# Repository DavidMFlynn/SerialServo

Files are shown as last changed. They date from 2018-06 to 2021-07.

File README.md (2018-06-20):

# SerialServo
Packet serial to R/C servo w/ absolute encoder
This is for one of my robot projects.
Features: TTL Serial interface, PWM output w/ 1/2 microsecond resolution, Current sensing, Absolute encoder SPI interface.
Features will be added as needed.
The Rev B PCB is being printed 6/19/2018

ToDo:

  Add params:

  Mode 4, Gripper control, closed value, open value
    Move toward close until reached or max current
    Open to open value
    OpenValue = FastRevVal, CloseValue = FastRevVal
    Speed is used for close only
    Open may be greater than or less than close, RevDirFlag?

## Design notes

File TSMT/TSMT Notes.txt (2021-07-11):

Terran Space Marine Transporter Notes (TSMT)
==========================================================================================
Body Jacks (Lifters)
	Home Switch is center of travel
	Positive rotation turns CW, CCW (Looking at the output shaft)
	Seek Home: Find the edge. Set zero. Go positive to turn the home switch off.
	Home sensor: OPB490P11Z, Active Low when light is blocked. (Positive, CW to unblock)
	Motor:iPower GBM5208H-200T a.k.a. GM5208-24, 11 pole pairs, 66 counts per rotation.
	Gear ratio 183:1, 12078 Counts per Rotation (33.55 per degree), 
		Safe zone: ±5368 (±160°) Counts from home
	
Addresses: (Serial Port/Device)
	01/03	Left front body mounted lifter (Sensored BLDC Drive, Position Mode)
	01/04	Left front track unit mounted lifter (Sensored BLDC Drive, Position Mode)
	01/05	Left front track unit drive (Sensored BLDC Drive, Torque Mode)
	
	01/06	Right front body mounted lifter (Sensored BLDC Drive, Position Mode)
	01/07	Right front track unit mounted lifter (Sensored BLDC Drive, Position Mode)
	01/08	Right front track unit drive (Sensored BLDC Drive, Torque Mode)
	
	??/??	Left rear body mounted lifter (Sensored BLDC Drive, Position Mode)
	??/??	Left rear track unit mounted lifter (Sensored BLDC Drive, Position Mode)
	??/??	Left rear track unit drive (Sensored BLDC Drive, Torque Mode)
	
	??/??	Right rear body mounted lifter (Sensored BLDC Drive, Position Mode)
	??/??	Right rear track unit mounted lifter (Sensored BLDC Drive, Position Mode)
	??/??	Right rear track unit drive (Sensored BLDC Drive, Torque Mode)
	
Lifter Motor Commutation
	OPB490P11Z (buffered, 10KΩ Pull Up)
	Red-1 Anode 470Ω to +5V
	Black-2 Cathode to GND
	White-3 Vcc to +5V
	Blue-4 Output (Low when blocked)
	Green-5 Ground to GND
		
	OPB492T11Z (inverted, 10KΩ Pull Up)
	Red-1 Anode 470Ω to +5V
	Black-2 Cathode to GND
	White-3 Vcc to +5V
	Blue-4 Output (High when blocked)
	Green-5 Ground to GND
	
	Sensored BLDC Motor Drive
	J4-1 +5V, RED 24AWG
	J4-2 GND, BLK 24AWG
	J4-3 Hall-U, YEL 24AWG
	J4-4 Hall-V, GRN 24AWG
	J4-5 Hall-W, BLU 24AWG
	
Home Switch
	J10-1 +5V, RED 24AWG
	J10-2 Signal, YEL 24AWG
	J10-3 GND, Black 24AWG

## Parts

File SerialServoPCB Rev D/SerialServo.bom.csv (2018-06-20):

Source | /Projects/SerialServo/SerialServoPCB/SerialServo.sch
Kicad Rev | Eeschema (5.0.0-rc2-80-gf95b77b)
Generated Date | Tuesday | June 19 | 2018 at 05:32:33 PM
Title | Serial Servo
Company | DMFE
Revision | B
Date Issue | 2018-06-19
Comment | TTL serial r/c servo controller
Reference | Value | Library | Library Ref
U1 | PIC16F1847-ISO | MCU_Microchip_PIC16 | PIC16F648A-ISO
J1 | Conn_01x04 | Connector_Generic | Conn_01x04
VR1 | L78L05_TO92 | Regulator_Linear | L78L05_TO92
VR2 | LM7805_TO220 | Regulator_Linear | LM7805_TO220
D5 | D | Device | D
SW1 | SW_Push | Switch | SW_Push
D1 | LED | Device | LED
R13 | 47K | Device | R
R12 | 1K0 | Device | R
C4 | 0.1uF | Device | C_Small
U2 | LM358A | Amplifier_Operational | LM358
D6 | D | Device | D
R6 | 0R200 1W | Device | R
C8 | 0.1uF | Device | C_Small
J4 | Conn_01x03 | Connector_Generic | Conn_01x03
R1 | 220R | Device | R
J3 | Conn_01x05 | Connector_Generic | Conn_01x05
SW2 | SW_Push | Switch | SW_Push
D2 | LED | Device | LED
R15 | 47K | Device | R
R14 | 1K0 | Device | R
SW3 | SW_Push | Switch | SW_Push
D3 | LED | Device | LED
R17 | 47K | Device | R
R16 | 1K0 | Device | R
C10 | 1uF | Device | C_Small
R10 | 47K | Device | R
R11 | 10K | Device | R
R9 | 100K | Device | R
R7 | 1K0 | Device | R
C7 | 0.1uF | Device | C_Small
C9 | 100uF | Device | CP1_Small
J2 | Conn_01x05 | Connector_Generic | Conn_01x05
C1 | 0.1uF | Device | C_Small
D4 | LED | Device | LED
R3 | 1K0 | Device | R
RV1 | 20K | Device | R_POT
C3 | 0.1uF | Device | C_Small
R2 | 1K0 | Device | R
R4 | 100K | Device | R
R5 | 10K | Device | R
C2 | 2.2uF | Device | CP1_Small
C5 | 2.2uF | Device | CP1_Small
C6 | 0.1uF | Device | C_Small
R21 | 1K0 | Device | R
J5 | Conn_01x03 | Connector_Generic | Conn_01x03
R18 | 1K0 | Device | R
J6 | Conn_01x03 | Connector_Generic | Conn_01x03
J7 | Conn_01x03 | Connector_Generic | Conn_01x03
R19 | 1K0 | Device | R
C12 | 0.1uF | Device | C_Small
R20 | 1K0 | Device | R
C13 | 0.1uF | Device | C_Small
C11 | 0.1uF | Device | C_Small
VR3 | LD1085 | Regulator_Linear | AZ1117-ADJ
J8 | Conn_01x02 | Connector_Generic | Conn_01x02
R22 | 120R | Device | R
R8 | RRR | Device | R
C14 | 0.1uF | Device | C_Small

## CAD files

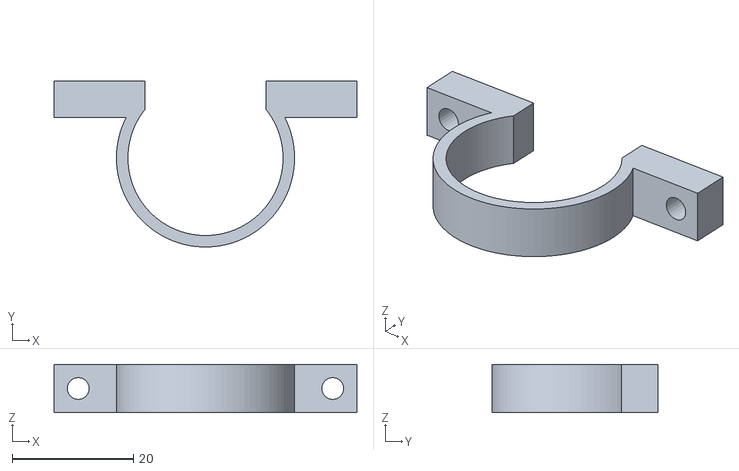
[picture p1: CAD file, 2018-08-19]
Case and Mount/Mount.stl
50.0 x 27.4 x 8.00

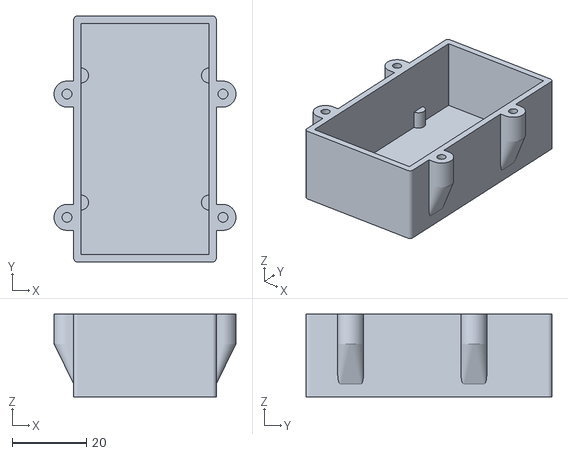
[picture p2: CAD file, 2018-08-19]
Case and Mount/Case.stl
49.0 x 66.2 x 22.3

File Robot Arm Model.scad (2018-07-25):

// ************************************************************
// Robot Arm Model
// David M. Flynn 
// Created: 6/11/2018
//
// Simple 3 degree of freedom arm
// Given an object (the blue sphere) at Obj_x,Obj_y,Obj_z
// Calculate the angle of the 3 joints (BaseRot_a,J1Rot_a,J2Rot_a)
// to place the object in the center of the gripper
// Recommended: Animation FPS=30, Steps=100 or more
// ************************************************************
//
// some usefull functions
function Oscillate(Dist) = (1-abs($t*2-1))*Dist; // move from 0 to Dist and back to 0 every cycle
function XY2Deg(X,Y) = -atan2(X,Y); // convert an X,Y to an angle 0=+y,90=-x,180/-180=-y,-90=+x
function Dist(X,Y) = sqrt(pow(X,2)+pow(Y,2)); // how far to x,y
//
//     C
//     /\
//   b/  \a
// A ----- B
//     c
// given the length of the sides calculate an inside angle
function AngleA(a,b,c) = acos( (pow(b,2)+pow(c,2)-pow(a,2)) / (2 * b * c));
function AngleB(a,b,c) = acos( (pow(a,2)+pow(c,2)-pow(b,2)) / (2 * a * c));
function AngleC(a,b,c) = acos( (pow(a,2)+pow(b,2)-pow(c,2)) / (2 * a * b));

//$t=0.0; // comment out to enable animation

// Position of object
Obj_x=Oscillate(200)-50;
Obj_y=Oscillate(100)+150;
Obj_z=Oscillate(100)+100; // from base plate or table surface

// The object.
translate([Obj_x,Obj_y,Obj_z]) color("Blue") sphere(d=20);

// Size of table base, just for show
	Table_h=3;
	Table_xy=200;

// Size of the joint, "A" has the servo and encoder, "B" is the turning part
	JointA_d=70;
	JointA_h=40;
	JointA_fn=14;
	JointB_d=90;
	JointB_h=38;
	JointB_fn=10;

// Length of the arm sections
	RodAB_l=240; // length from J1 to J2
	RodBC_l=230; // length from J2 center line to moddle of gripper
	
Tube_d=19;
BaseToJ1_z=JointB_d/2;
BaseToJ1_x=-JointA_h/2;
J1_CL_z=JointA_h+JointB_h+BaseToJ1_z;

module DrawJoint(Rot_a=0){
	// Base
	cylinder(d=JointA_d,h=JointA_h,$fn=JointA_fn);
	
	// the turning part
	translate([0,0,JointA_h]) rotate([0,0,Rot_a]){
		cylinder(d=JointB_d,h=JointB_h,$fn=JointB_fn);
		
		// Indicator: Which way am I pointing?
		translate([0,JointB_d/2-10,JointB_h]) rotate([0,0,-30]) color("Tan") cylinder(d=10,h=1,$fn=3);
	}
} // DrawJoint

module DrawBase(Rot_a=0){
	//translate([0,0,Table_h/2]) cylinder(d=Table_xy,h=Table_h,$fn=8,center=true);
	translate([0,0,-70]) cylinder(d1=120,d2=80,h=70,$fn=12);
	DrawJoint(Rot_a=Rot_a);
} // DrawBase

// do the math
BaseRot_a=XY2Deg(Obj_x,Obj_y);
Adj_z=Obj_z-J1_CL_z; // Z relitive to J1 rotation center
d=Dist(Obj_x,Obj_y);  // distance in XY plane
hypJ2=Dist(d,Adj_z); // end to J1 distance
Targ_a=XY2Deg(d,Adj_z);
J2Rot_a=180-AngleC(RodAB_l,RodBC_l,hypJ2);
J1Ang_B=AngleB(RodAB_l,RodBC_l,hypJ2);
J1Rot_a=Targ_a+J1Ang_B;

// Show the angles to the user.
echo(BaseRot=BaseRot_a);
echo(J1Rot_a=J1Rot_a);
echo(J2Rot_a=J2Rot_a);

// Draw the arm
module Draw3DoFArm(BaseRot_a=BaseRot_a,J1Rot_a=J1Rot_a,J2Rot_a=J2Rot_a){
	DrawBase(Rot_a=BaseRot_a);

	translate([0,0,JointA_h+JointB_h]) rotate([0,0,BaseRot_a]) translate([BaseToJ1_x,0,BaseToJ1_z])
		rotate([0,90,0]) rotate([0,0,90]){
			
		// the joint attached to the rotating base	
		DrawJoint(Rot_a=J1Rot_a);
			
		rotate([0,0,J1Rot_a]) translate([0,0,JointA_h+JointB_h/2]) {
			// rod connection J1 and J2
			rotate([-90,0,0]) color("Silver") cylinder(d=Tube_d,h=RodAB_l);
			translate([0,RodAB_l,JointA_h/2])rotate([0,180,0]){
				// mid-arm joint
				DrawJoint(Rot_a=J2Rot_a);
				// rod from J2 to middle of the gripper
				translate([0,0,JointA_h+JointB_h/2])rotate([0,0,J2Rot_a]){
					rotate([-90,0,0]) color("Silver") cylinder(d=Tube_d,h=RodBC_l);
}}}}}

//Draw3DoFArm();
//Draw3DoFArm(0,0,0);

// Lo-Rez Arm parts
module LoRezBase(){
	cylinder(d1=120,d2=80,h=70,$fn=12);
	translate([0,0,70]) cylinder(d=JointA_d,h=JointA_h,$fn=JointA_fn);
} // LoRezBase

//LoRezBase(); // height is 70+JointA_h

module LoRezJoint(){
	cylinder(d=JointB_d,h=JointB_h,$fn=JointB_fn);
		
		// Indicator: Which way am I pointing?
		translate([0,JointB_d/2-11,JointB_h]) rotate([0,0,-30]) color("Tan") cylinder(d=10,h=1,$fn=3);
} // LoRezJoint

//LoRezJoint();

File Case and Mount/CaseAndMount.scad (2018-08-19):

// ******************************************************
// Case and Mount for Serial Servo Rev B PCB
// by Dave Flynn
// Created:8/13/2018
// Revision: 1.0.1 8/19/2018
// Units: mm
// ******************************************************
// History:
// 1.0.1 8/19/2018 Moved mounting locations.
// 1.0.0 8/13/2018 First Code
// ******************************************************
// Notes:
// ******************************************************
// for STL output
// SSCaseBack();
// TubeMount();
// ******************************************************

include<CommonStuffSAEmm.scad>

$fn=90;
Overlap=0.05;
IDXtra=0.2;

PCB_x=34.4;
PCB_y=62.2;
PCB_z=1.8; // board only
PCB_Back_Parts_z=5;
PCB_Front_Parts_z=13.5;

CaseWall=2;
RC_BoltSpace=42;
Tube_OD=25.4;
RC_Spacer_h=4;

module RoundRect(X=60,Y=40,Z=10,R=5){
	hull(){
		translate([-X/2+R,-Y/2+R,0]) cylinder(r=R,h=Z);
		translate([X/2-R,-Y/2+R,0]) cylinder(r=R,h=Z);
		translate([-X/2+R,Y/2-R,0]) cylinder(r=R,h=Z);
		translate([X/2-R,Y/2-R,0]) cylinder(r=R,h=Z);
		
	} // hull
	
} // RoundRect

module SSCaseBack(){
	PCB_Clip_y=14;
	BoltBoss_yt=19;
	BoltBoss_yb=10;
	
	Case_h=PCB_Back_Parts_z+PCB_z+PCB_Front_Parts_z+CaseWall;
	
	module BoltBoss(XTra=1){
		difference(){
			hull(){
				translate([2.5+XTra,-3.5,0]) cube([Overlap,7,Case_h]);
				translate([0,0,Case_h-8]) cylinder(d=7,h=8);
			} // hull
			translate([0,0,Case_h])  Bolt4Hole(depth=9);
		} // diff
	}// BoltBoss
	
	difference(){
		RoundRect(X=PCB_x+CaseWall*2,Y=PCB_y+CaseWall*2,Z=Case_h,R=1);
		
		translate([0,0,CaseWall]) RoundRect(X=PCB_x,Y=PCB_y,Z=PCB_Back_Parts_z+PCB_z+PCB_Front_Parts_z+2+Overlap,R=0.1);
		
		
	} // diff
	// Bolts
	translate([-RC_BoltSpace/2,PCB_y/2-BoltBoss_yt,0])  BoltBoss(XTra=1);
	translate([RC_BoltSpace/2,PCB_y/2-BoltBoss_yt,0]) rotate([0,0,180])  BoltBoss(XTra=1);
	translate([RC_BoltSpace/2,-PCB_y/2+BoltBoss_yb,0]) rotate([0,0,180]) BoltBoss(XTra=1);
	translate([-RC_BoltSpace/2,-PCB_y/2+BoltBoss_yb,0])  BoltBoss(XTra=1);
	
	// bottom stops
	translate([-PCB_x/2,-PCB_y/2+PCB_Clip_y,Overlap]) cylinder(r=CaseWall,h=CaseWall+PCB_Back_Parts_z);
	translate([-PCB_x/2,PCB_y/2-PCB_Clip_y,Overlap]) cylinder(r=CaseWall,h=CaseWall+PCB_Back_Parts_z);
	translate([PCB_x/2,-PCB_y/2+PCB_Clip_y,Overlap]) cylinder(r=CaseWall,h=CaseWall+PCB_Back_Parts_z);
	translate([PCB_x/2,PCB_y/2-PCB_Clip_y,Overlap]) cylinder(r=CaseWall,h=CaseWall+PCB_Back_Parts_z);
	
	/*
	translate([0,0,CaseWall+PCB_Back_Parts_z+PCB_z+IDXtra]){
	translate([-PCB_x/2,-PCB_y/2+PCB_Clip_y,Overlap]) cylinder(r1=CaseWall,r2=0.5,h=CaseWall+PCB_Back_Parts_z);
	translate([-PCB_x/2,PCB_y/2-PCB_Clip_y,Overlap]) cylinder(r1=CaseWall,r2=0.5,h=CaseWall+PCB_Back_Parts_z);
	translate([PCB_x/2,-PCB_y/2+PCB_Clip_y,Overlap]) cylinder(r1=CaseWall,r2=0.5,h=CaseWall+PCB_Back_Parts_z);
	translate([PCB_x/2,PCB_y/2-PCB_Clip_y,Overlap]) cylinder(r1=CaseWall,r2=0.5,h=CaseWall+PCB_Back_Parts_z);
	}
	/**/
} // SSCaseBack

//SSCaseBack();



module TubeMount(){
	TM_h=8;
	
	difference(){
		union(){
			cylinder(d=Tube_OD+4,h=TM_h);
			translate([-(RC_BoltSpace+8)/2,Tube_OD/2-6,0]) cube([RC_BoltSpace+8,6,TM_h]);
			
			/*
			// Spacers
			translate([RC_BoltSpace/2,Tube_OD/2+RC_Spacer_h,TM_h/2])rotate([90,0,0])hull()
			{
				cylinder(d=7,h=RC_Spacer_h+Overlap);
				translate([3,-TM_h/2,0])cube([1,TM_h/2+3.5,7]);
				translate([-3.5,-TM_h/2,0])cube([TM_h/2+3.5,1,7]);
			}
			mirror([1,0,0])
			translate([RC_BoltSpace/2,Tube_OD/2+RC_Spacer_h,TM_h/2])rotate([90,0,0])hull()
			{
				cylinder(d=7,h=RC_Spacer_h+Overlap);
				translate([3,-TM_h/2,0])cube([1,TM_h/2+3.5,7]);
				translate([-3.5,-TM_h/2,0])cube([TM_h/2+3.5,1,7]);
			}
			*/
		} // union
		
		// Tube cut
		translate([-10,0,-Overlap]) cube([20,20,TM_h+Overlap*2]);
		
		// Bolts
		translate([RC_BoltSpace/2,Tube_OD/2+RC_Spacer_h,TM_h/2])rotate([-90,0,0])  Bolt4ClearHole();
		translate([-RC_BoltSpace/2,Tube_OD/2+RC_Spacer_h,TM_h/2])rotate([-90,0,0])  Bolt4ClearHole();
		
		// Tube
		translate([0,0,-Overlap]) cylinder(d=Tube_OD+IDXtra,h=TM_h+Overlap*2);
	} // diff
	
} // TubeMount

//TubeMount();

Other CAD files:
Case and Mount/CommonStuffSAEmm.scad

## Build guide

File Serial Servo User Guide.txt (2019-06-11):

TTL Serial connected to a USB to Serial.

Uses TTL serial from a USB to 5 volt TTL serial converter to control several R/C servos.
Packet serial is used to give each servo a unique address. Operation modes include basic
 servo position (open loop) w/ current limit and monitoring.  Mode 3 uses an absolute
 magnetic encoder (AEAT-6012) to close the position loop.

Communication:
38,400 baud, 8 data, 1 stop, no parity.
To connect multiple Serial Servos to a single connection add a 4.7KΩ resistor to the
 Rx line of the USB to serial converter, a.k.a. the common Tx line of the Serial Servos.

Packet Serial:
All packets are 6 bytes w/o optional sync bytes and checksum:
Source Address, Destination Address and 4 data bytes
or
0xDD,0xDD,Source Address, Destination Address and 4 data bytes, Checksum 
(XOR of Source Addr, Dest Addr, 4 Data bytes)

Default master address is 1
Default slave address is 2

All commands return something. Some return a data packet (Slave,Master,Data0,Data1,Data2,Data3,CSum),
others return only a single byte (0xFF) as an acknowledgment 

Mode:
------------------------------------------------------------------------------------------
Mode 0: (LED 1 = off) servo test mode, copy AN4 Pot value to servo.
Mode 1: (LED 1 = 1 flash) servo and encoder test mode, AN4 Pot value - EncoderVal to servo dir.
Mode 2: Basic Serial Servo, output servo pulse of CmdPos * 0.5uS.
Mode 3: Absolute encoder position control.
Mode 4: Gripper force control.

Commands:
kCmd_SetMode(0x81)	+1 data (SysMode), return ACK
kCmd_GetMode(0x01)
kCmd_SetCmdPos(0x82)	+2 data (ssCmdPos), return ACK
kCmd_GetCmdPos(0x02)
kCmd_SetMaxI(0x83)	+1 data (ssMaxI), return ACK
kCmd_GetMaxI(0x03)
kCmd_SetFFwd(0x84)	+2 data (ServoFastForward), return ACK
kCmd_GetFFwd(0x04)
kCmd_SetFRev(0x85)	+2 data (ServoFastReverse), return ACK
kCmd_GetFRev(0x05)
kCmd_SetMin_uS(0x86)	+2 data (ServoMin_uS), return ACK
kCmd_GetMin_uS(0x06)
kCmd_SetMax_uS(0x87)	+2 data (ServoMax_uS), return ACK
kCmd_GetMax_uS(0x07)
kCmd_SetRevDir(0x88)	+1 data (ssReverseDir), return ACK
kCmd_GetRevDir(0x08)
kCmd_SetEnaOvrCur(0x89)  +1 data (ssEnableOverCur), return ACK
kCmd_GetEnaOvrCur(0x09)
kCmd_Set_HighZ_TX(0x8A)  +1 data (ssEnableHighZTZ), return ACK
kCmd_Get_HighZ_TX(0x0A)
kCmd_SetStopCenter(0x8B) +2 data (ServoStopCenter), return ACK
kCmd_GetStopCenter(0x0B)
kCmd_SetSpeed(0x8C)      +1 data (ServoSpeed), return ACK
kCmd_GetSpeed(0x0C)
kCmd_SetUseIdleCenter(0x8D) +1 data (ssMode3IdleCenter), return ACK
kCmd_GetUseIdleCenter(0x0D)
kCmd_SetDeadBand(0x8E) +1 data (DeadBand), return ACK
kCmd_GetDeadBand(0x0E)
kCmd_SetUseFastPWM(0x8F) +1 data (ssEnableFastPWM), return ACK
kCmd_GetUseFastPWM(0x0F)
kCmd_SetGripI(0xB1)	+1 data (ssGripI), return ACK
kCmd_GetGripI(0x21)
kCmd_SetAuxConfig(0xB2)  +2 data (AuxNum,Value), return ACK
kCmd_GetAuxConfig(0x22)  +1 data (AuxNum)
kCmd_SetAuxNValue(0xB3)  +2 data (AuxNum,Value), return ACK
kCmd_GetAuxNValue(0x23)  (AuxN,ValueL,ValueH)
kCmd_SetEncoderOffset(0xB4) +2 data (EncoderOffset), return ACK
kCmd_GetEncoderOffset(0x24)
;
kCmd_GetI(0x91)	return Cur_AN0
kCmd_GetEnc(0x92)	return EncoderVal
kCmd_GetEncAbs(0x93)	return EncoderAccum
kCmd_SaveParams(0x94)	Save all eeprom params, return ACK
kCmd_RestoreParams(0x95)  Copy to ram, return ACK
kCmd_GetBattVolts(0x96)  return Cur_AN7
kCmd_GetCalPot(0x97)	 return Cur_AN4
kCmd_GetStatus(0x98)    return ssStatus:4
;
; these commands save params and return a 0,0,0,0 packet with the new address
kCmd_SetMasterAddr(0xA1) +1 data, return a zero packet
kCmd_SetSlaveAddr(0xA2) +1 data, return a zero packet
kCmd_SendIDString(0xAA) Special packet (0xDD, 0xDD, 0x01, 0x02, 0xAA, 0x00, 0x00, 0x00, checksum) returns "DMFE Serial Servo\n"

Aux(0,1,2)Config byte		Data to/from
0	Default/Unused	none
1	LED/Btn	LED Flashes 0..9,15 (15=on)/High nibble=Flashes, Low = Btn
2	Digital Input	none/Bit(0/1)
3	Digital Output	Bit(0/1)/Bit(0/1)
4	Analog Input	none/10 bit ADC value
5	Home Switch/Digital Input none/Bit(0/1)
6	Fwd Limit Switch/Digital Input none/Bit(0/1)
7	Rev Limit Switch/Digital Input none/Bit(0/1)

Encoder Cable
--------------------------------------------
WM1723-ND   Connector Housing 5pos 1.25mm 
WM12935-ND  Wires w/ pre-crimped terminals
WM2903-ND   Connector Housing 5 pos .100
2510-ND     Connector Terminal Tin
24 AWG style 1007, Red, Yellow, Black, Green, Blue

J2 Pin        Wire      Encoder
1 VDD         Red       1 5V Supply Voltage
2 CSn Output  Yellow    2 Chip Select active low Input
3 VSS         Black     3 Supply Ground
4 CLK Output  Green     4 Serial Clock Input
5 DO  Input   Blue      5 DO Serial Data Output

Serial Servo PCB Rev B Bill of Material
-----------------------------------------------------------------------------------------------
R1	Resistor 220Ω SMT 0805
R2,R3,R7,R12,R14,
R16,R18,R19,R20,R21	Resistor 1.00KΩ SMT 0805
R4,R9	Resistor 100KΩ SMT 0805
R5,R11	Resistor 10.0KΩ SMT 0805
R6	Resistor 0.2Ω 1W SMT 2512
R8	Resistor SMT 0805
R10	Resistor 47KΩ SMT 0805
R13	omitted from Rev B
R22	Resistor 120Ω  SMT 0805
RV1	Potentiometer 20KΩ

C1,C3,C4,C6,C7,
C8,C11,C12,C13,C14	Capacitor 0.1uf 50V SMT 0805
C2,C5	Capacitor 2.2uf 25V Electrolytic
C9	Capacitor 220uf 25V Electrolytic
C10	Capacitor 1.0uf 25V SMT 0805

U1	PIC16F1847 SMT SO-18
U2	LM358AM SMT SO-8

VR1	Linear Voltage Regulator L78L05 TO-92
VR2	6V 1.5A In-Gnd-Out (optional)
VR3	Adj D-Pak Adj-Out-In (optional)
D5	Diode SMA Rectifier (logic power)
D6	Diode SMA Rectifier (servo power optional)

J1	Connector 4 Pos (power & IO)
J2	Connector 5 Pos (encoder)
J3	Connector 5 Pos (programming optional)
J4	Connector 3 Pos (Servo)
J5,J6,J7	Connector 3 Pos (Digital IO/Analog In optional)
J8	Jumper Servo Power Regulator Bypass (optional)

Options (Note: Some options are mutually exclusive)
------------
AN1/RA1:	LED install D1, R12
	Push-Button Switch R13,SW1
	Analog input R18,C11,J5
	Digital I/O R13,R18,C11,J5

AN2/RA2:	LED install D2, R14
	Push-Button Switch R15,SW2
	Analog input R19,C12,J6
	Digital I/O R15,R19,C12,J6

AN3/RA3:	LED install D3, R16
	Push-Button Switch R17,SW3
	Analog input R20,C13,J7
	Digital I/O R17,R20,C13,J7
	
R13,R15,R17 Pull-Ups for digital inputs
C11,C12,C13 Integration for analog/digital input

Servo Power:	6V 1.5A VR2,D6,C5,C8,C9
	Adj 3A, VR3,D6,C5,C8,C9,R8,R22
	Direct C8,C9,J8
	D6 may be Jumped
	
Battery Voltage:	R2,R4,R5,C3,U2B

Servo Current:	R7,R9,R10,R11,C7,C10,U2A

System LED:	R3,D4

Encoder:	C1,J2

Other notes:
---------------------------
Test to do: A,B,I quadrature encoder interface. Auto zero on I?
Add: Analog inputs to Aux 0,1,2
Add: Multi-rotation absolute encoder support with limit and home switches.
Add: ABI encoder flag, Multi-rotation flag.
Add: Encoder offset for absolute encoder. (Enc + Offset) mod 4096
      Get/Set, Default = 0x0000

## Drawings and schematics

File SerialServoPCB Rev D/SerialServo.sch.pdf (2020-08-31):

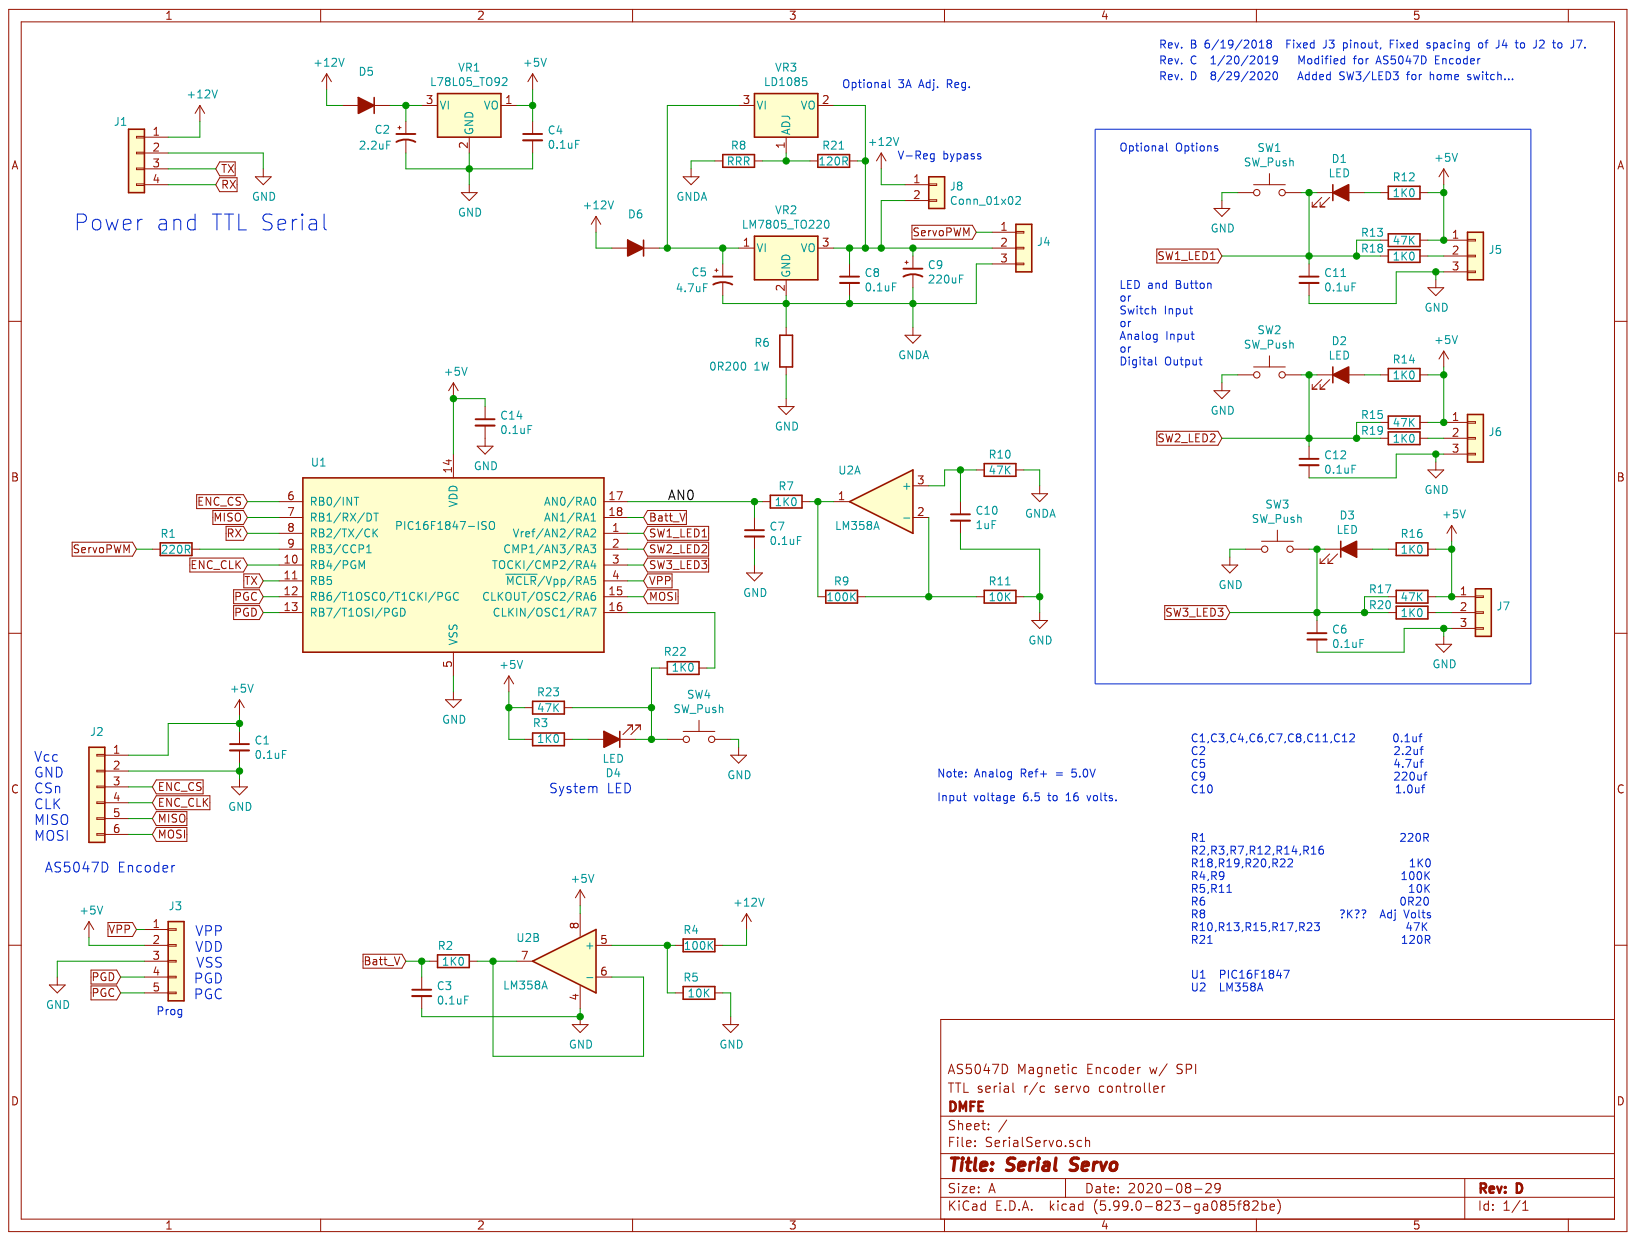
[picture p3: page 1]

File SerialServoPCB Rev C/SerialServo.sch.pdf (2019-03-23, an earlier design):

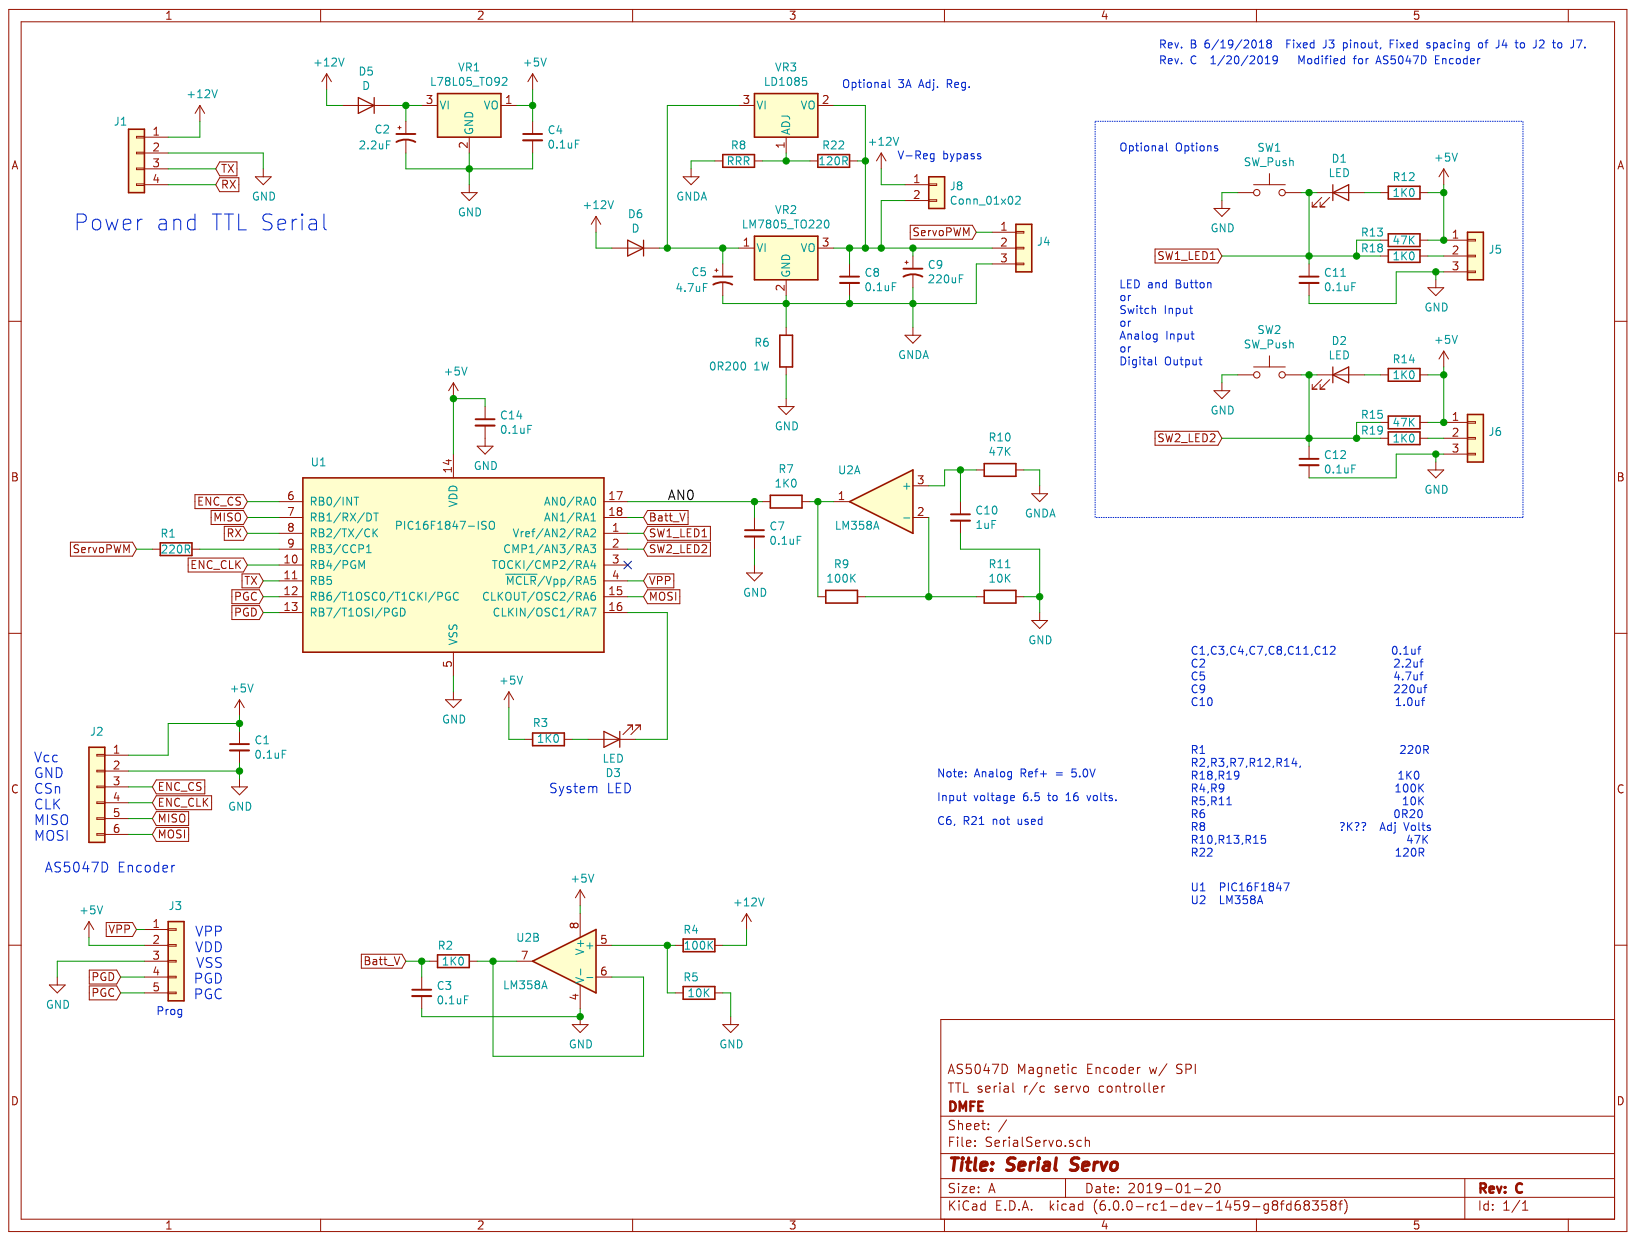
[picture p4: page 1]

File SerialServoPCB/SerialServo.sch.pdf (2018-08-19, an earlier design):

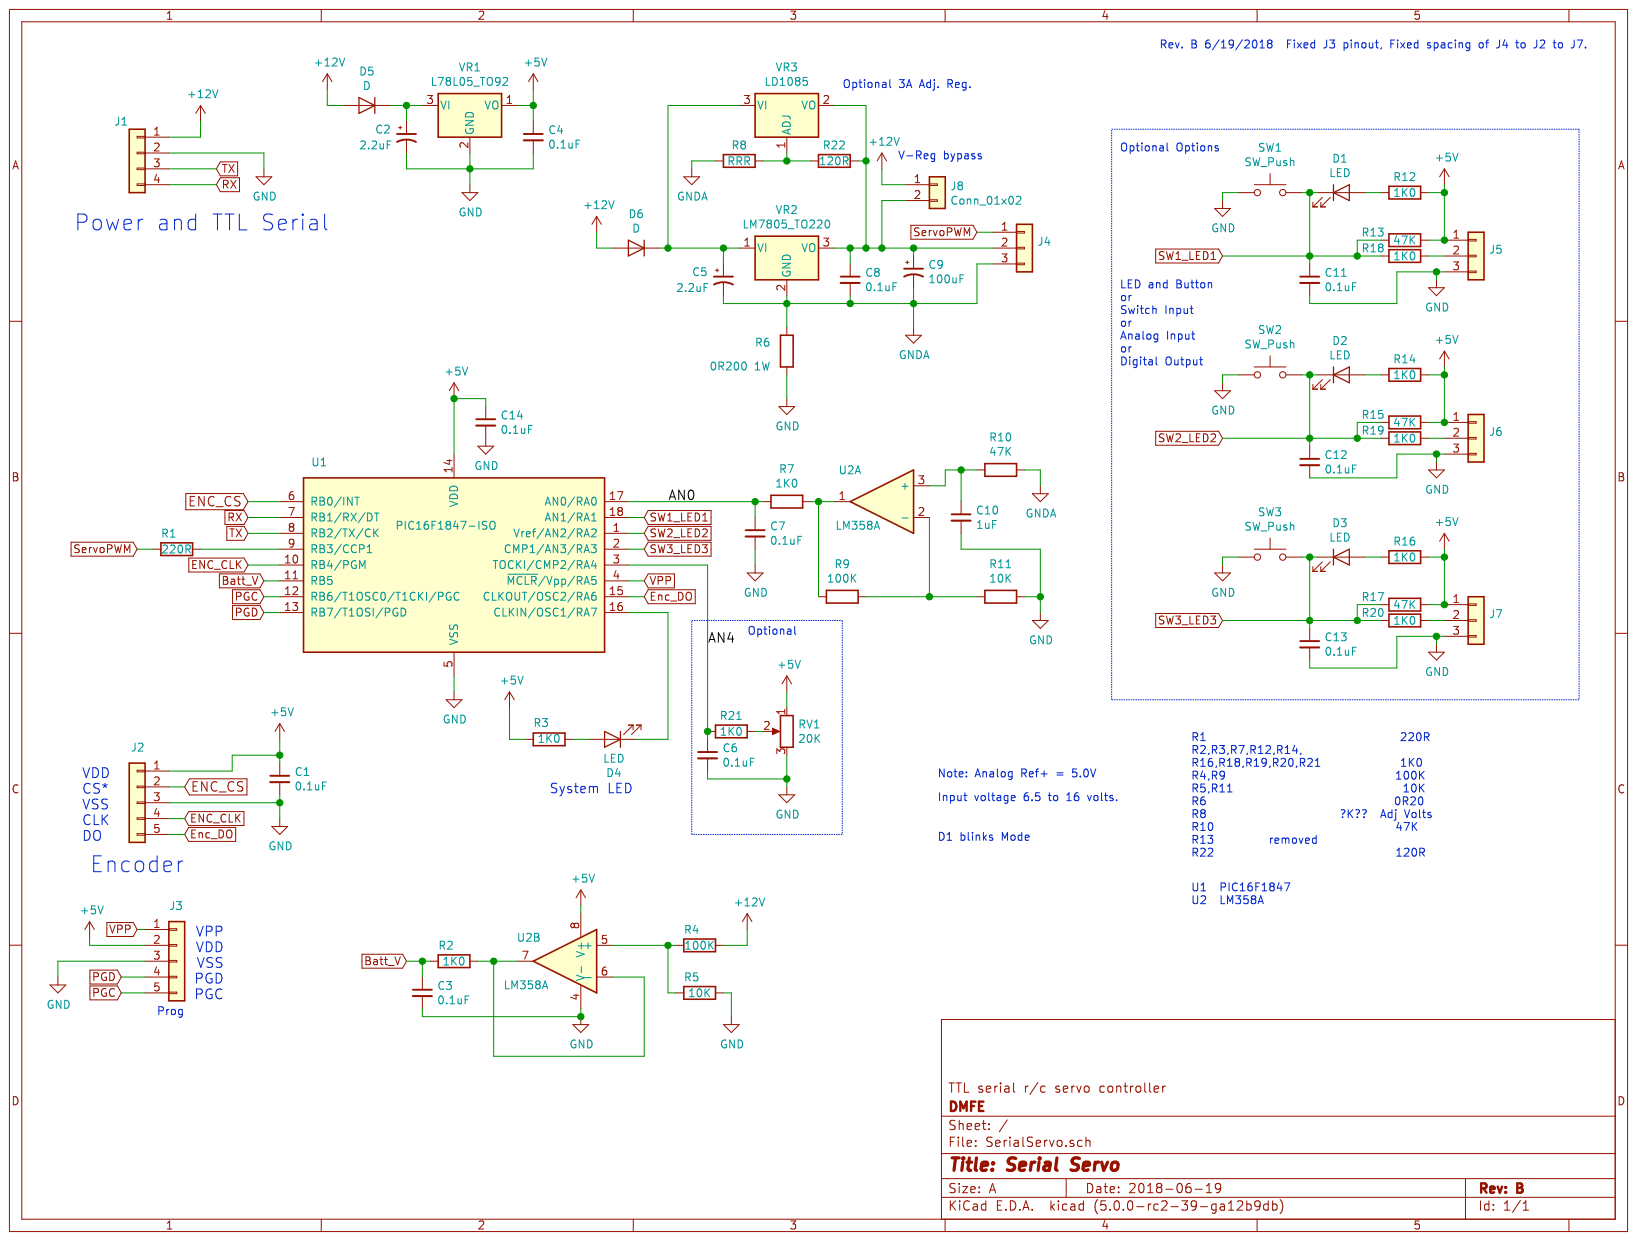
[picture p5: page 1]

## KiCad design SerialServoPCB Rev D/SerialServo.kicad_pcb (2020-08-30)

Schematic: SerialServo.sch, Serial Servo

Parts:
C1, C3, C4, C6, C7, C8, C11, C12, C14: 0.1uF; C_0805_2012Metric
C2: 2.2uF; CP_Radial_D5.0mm_P2.00mm
C5: 4.7uF; CP_Radial_D5.0mm_P2.00mm
C9: 220uF; CP_Radial_D8.0mm_P5.00mm
C10: 1uF; C_0805_2012Metric
D1, D2, D3, D4: LED; LED_0805_2012Metric_Pad1.15x1.40mm_HandSolder
D5, D6: SMA Diode; D_SMA
J1: Conn_01x04; Molex_KK-254_AE-6410-04A_1x04_P2.54mm_Vertical
J2: Conn_01x06; Molex_KK-254_AE-6410-06A_1x06_P2.54mm_Vertical
J3: Conn_01x05; PinHeader_1x05_P2.54mm_Vertical
J4, J5, J6, J7: Conn_01x03; Molex_KK-254_AE-6410-03A_1x03_P2.54mm_Vertical
J8: Conn_01x02; PinHeader_1x02_P2.54mm_Vertical
R1: 220R; R_0805_2012Metric
R2, R3, R7, R12, R14, R16, R18, R19, R20: 1K0; R_0805_2012Metric
R4, R9: 100K; R_0805_2012Metric
R5, R11: 10K; R_0805_2012Metric
R6: 0R200 1W; R_2512_6332Metric_Pad1.52x3.35mm_HandSolder
R8: RRR; R_0805_2012Metric
R10, R13, R15, R17: 47K; R_0805_2012Metric
R21: 120R; R_0805_2012Metric
SW1, SW2, SW3: SW_Push; SW_SPST_FSMSM
U1: PIC16F1847-ISO; SOIC-18W_7.5x11.6mm_P1.27mm
U2: LM358A; SOIC-8_3.9x4.9mm_P1.27mm
VR1: L78L05_TO92; TO-92L_Wide
VR2: LM7805_TO220; TO-263-3_TabPin2
VR3: LD1085; TO-263-3_TabPin2

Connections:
+5V: C1.1, C4.1, C14.1, J2.1, J3.2, J5.1, J6.1, J7.1, R3.2, R12.1, R13.1, R14.1, R15.1, R16.1, R17.1, U1.14, U2.8, VR1.1
+12V: D5.2 (A), D6.2 (A), J1.1, J8.1, R4.1
/AN0: C7.1, R7.2, U1.17
Batt_V: C3.1, R2.2, U1.18
ENC_CLK: J2.4, U1.10
ENC_CS: J2.3, U1.6
GND: C1.2, C2.2, C3.2, C4.2, C6.2, C7.2, C10.2, C11.2, C12.2, C14.2, J1.2, J2.2, J3.3, J5.3, J6.3, J7.3, R5.1, R6.1, R11.1, SW1.1, SW2.1, SW3.1, U1.5, U2.4, VR1.2
GNDA: C5.2, C8.2, C9.2, J4.3, R6.2, R8.2, R10.1, VR2.2 (GND)
MISO: J2.5, U1.7
MOSI: J2.6, U1.15
unnamed: C2.1, D5.1 (K), VR1.3
unnamed: C5.1, D6.1 (K), VR2.1 (VI), VR3.3
unnamed: C8.1, C9.1, J4.2, J8.2, R21.1, VR2.3 (VO), VR3.2
unnamed: C10.1, R10.2, U2.3
unnamed: D1.2 (A), R12.2
unnamed: D2.2 (A), R14.2
unnamed: D3.2 (A), R16.2
unnamed: D4.1 (K), U1.16
unnamed: D4.2 (A), R3.1
unnamed: J5.2, R18.1
unnamed: J6.2, R19.1
unnamed: J7.2, R20.1
unnamed: R1.1, U1.9
unnamed: R2.1, U2.6, U2.7
unnamed: R4.2, R5.2, U2.5
unnamed: R7.1, R9.2, U2.1
unnamed: R9.1, R11.2, U2.2
unnamed: R8.1, R21.2, VR3.1
PGC: J3.5, U1.12
PGD: J3.4, U1.13
RX: J1.4, U1.8
SW1_LED1: C11.1, D1.1 (K), R13.2, R18.2, SW1.2, U1.1
SW2_LED2: C12.1, D2.1 (K), R15.2, R19.2, SW2.2, U1.2
SW3_LED3: C6.1, D3.1 (K), R17.2, R20.2, SW3.2, U1.3
ServoPWM: J4.1, R1.2
TX: J1.3, U1.11
VPP: J3.1, U1.4

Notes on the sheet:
Vcc GND CSn CLK MISO MOSI
Power and TTL Serial
AS5047D Encoder
Prog
VPP VDD VSS PGD PGC
System LED
Optional 3A Adj. Reg.
V-Reg bypass
Note: Analog Ref+ = 5.0V
Input voltage 6.5 to 16 volts.
Optional Options
LED and Button or Switch Input or Analog Input or Digital Output
Rev. B 6/19/2018 Fixed J3 pinout, Fixed spacing of J4 to J2 to J7.
Rev. C 1/20/2019 Modified for AS5047D Encoder
Rev. D 8/29/2020 Added SW3/LED3 for home switch...
C1,C3,C4,C6,C7,C8,C11,C12 0.1uf C2 2.2uf C5 4.7uf C9 220uf C10 1.0uf
R1 220R R2,R3,R7,R12,R14,R16 R18,R19,R20 1K0 R4,R9 100K R5,R11 10K R6 0R20 R8 ?K?? Adj Volts R10,R13,R15,R17 47K R21 120R
U1 PIC16F1847 U2 LM358A

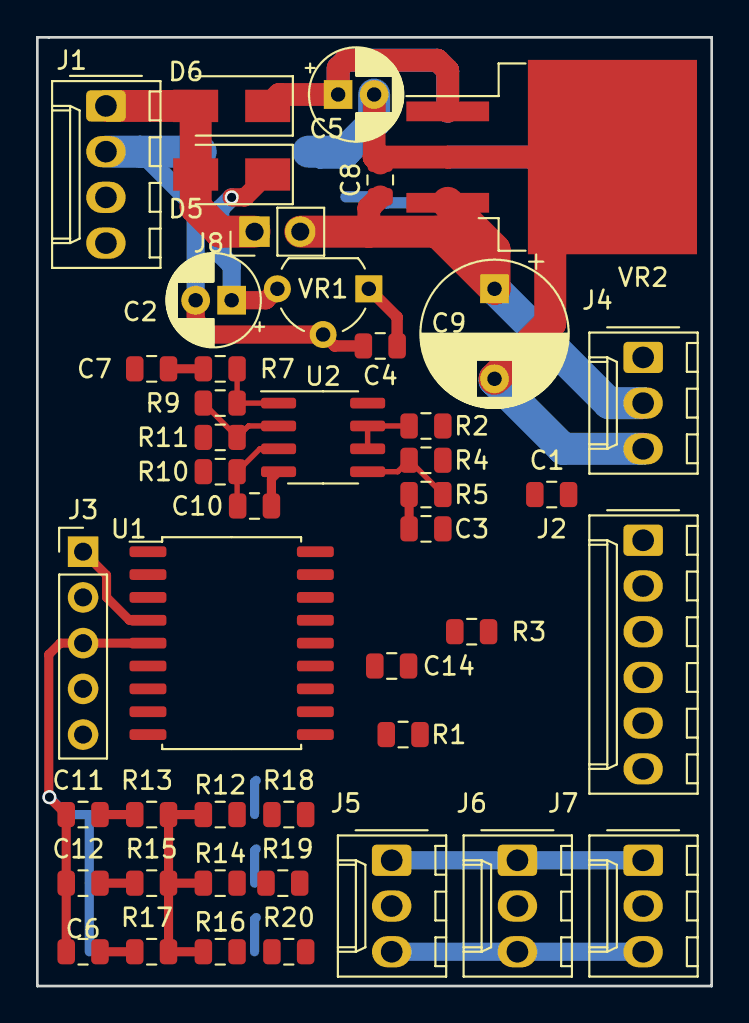
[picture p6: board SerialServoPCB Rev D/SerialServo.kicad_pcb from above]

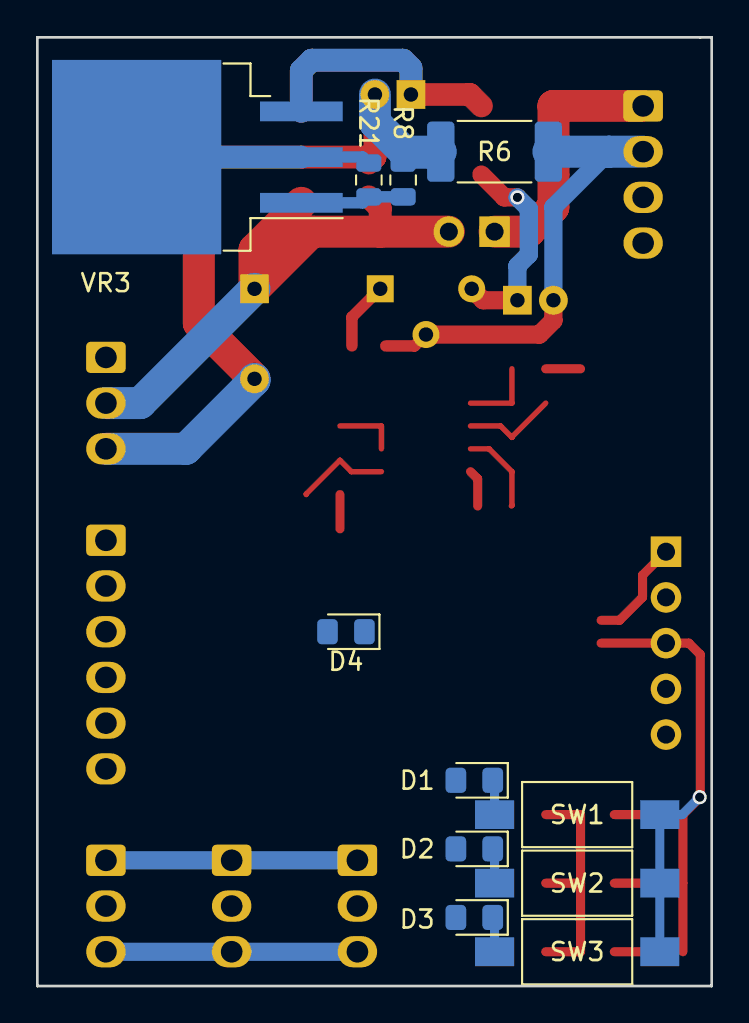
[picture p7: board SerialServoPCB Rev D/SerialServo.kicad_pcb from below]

Board: 2 copper layers, 37.5 x 52.7 mm, 56 parts (11 on the bottom side), 37 nets.

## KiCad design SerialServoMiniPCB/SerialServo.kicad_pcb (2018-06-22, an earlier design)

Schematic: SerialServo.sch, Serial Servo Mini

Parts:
C1, C3, C4, C5, C7, C8: 0.1uF; C_0805_2012Metric_Pad1.29x1.40mm_HandSolder
C2, C6: 2.2uF; CP_Radial_D5.0mm_P2.00mm
C9: 100uF; CP_Radial_D8.0mm_P5.00mm
C10: 1uF; C_0805_2012Metric_Pad1.29x1.40mm_HandSolder
D1, D3: D; D_SMA_Handsoldering
D2: LED; LED_0805_2012Metric_Pad1.12x1.40mm_HandSolder
J1: Conn_01x04; Molex_KK-254_AE-6410-04A_1x04_P2.54mm_Vertical
J2: Conn_01x05; Molex_KK-254_AE-6410-05A_1x05_P2.54mm_Vertical
J3: Conn_01x05; PinHeader_1x05_P2.54mm_Vertical
J4: Conn_01x03; Molex_KK-254_AE-6410-03A_1x03_P2.54mm_Vertical
R1: 220R; R_0805_2012Metric_Pad1.29x1.40mm_HandSolder
R2, R3, R7: 1K0; R_0805_2012Metric_Pad1.29x1.40mm_HandSolder
R4, R8: 100K; R_0805_2012Metric_Pad1.29x1.40mm_HandSolder
R5, R10: 10K; R_0805_2012Metric_Pad1.29x1.40mm_HandSolder
R6: 0R200 1W; R_2512_6332Metric_Pad1.49x3.40mm_HandSolder
R9: 47K; R_0805_2012Metric_Pad1.29x1.40mm_HandSolder
U1: PIC16F1847-ISO; SOIC-18W_7.5x11.6mm_P1.27mm
U2: LM358A; SOIC-8_3.9x4.9mm_P1.27mm
VR1: L78L05_TO92; TO-92L_Wide
VR2: LM7805_TO220; TO-263-3_TabPin2

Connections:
+5V: C1.1, C4.1, C5.1, J2.1, J3.2, R3.2, U1.14 (VDD), U2.8 (V+), VR1.1 (VO)
+12V: D1.2, D3.2, J1.1, R4.1
/AN0: C7.1, R7.2, U1.17 (AN0/RA0)
Batt_V: C3.1, R2.2, U1.11 (RB5)
ENC_CLK: J2.4, U1.10 (RB4/PGM)
ENC_CS: J2.2, U1.6 (RB0/INT)
Enc_DO: J2.5, U1.15 (CLKOUT/OSC2/RA6)
GND: C1.2, C2.2, C3.2, C4.2, C5.2, C7.2, C10.2, J1.2, J2.3, J3.3, R5.1, R6.1, R10.1, U1.5 (VSS), U2.4 (V-), VR1.2 (GND)
GNDA: C6.2, C8.2, C9.2, J4.3, R6.2, R9.1, VR2.2
unnamed: C2.1, D1.1, VR1.3 (VI)
unnamed: C6.1, D3.1, VR2.1
unnamed: C8.1, C9.1, J4.2, VR2.3
unnamed: C10.1, R9.2, U2.3 (+)
unnamed: D2.1, U1.16 (CLKIN/OSC1/RA7)
unnamed: D2.2, R3.1
unnamed: R1.1, U1.9 (RB3/CCP1)
unnamed: R2.1, U2.6 (-), U2.7
unnamed: R4.2, R5.2, U2.5 (+)
unnamed: R7.1, R8.2, U2.1
unnamed: R8.1, R10.2, U2.2 (-)
PGC: J3.5, U1.12 (RB6/T1OSC0/T1CKI/PGC)
PGD: J3.4, U1.13 (RB7/T1OSI/PGD)
RX: J1.4, U1.7 (RB1/RX/DT)
ServoPWM: J4.1, R1.2
TX: J1.3, U1.8 (RB2/TX/CK)
VPP: J3.1, U1.4 (~MCLR~/Vpp/RA5)

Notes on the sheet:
Prog
VDD VPP VSS PGD PGC
Encoder
VDD CS* VSS CLK DO
System LED
Note: Analog Ref+ = 5.0V
Input voltage 6.5 to 16 volts.
Rev. B 6/19/2018 Fixed J3 pinout, Fixed spacing of J4 to J2 to J7.
Power and TTL Serial
Mini n/c 6/21/2018 Removed stuff.

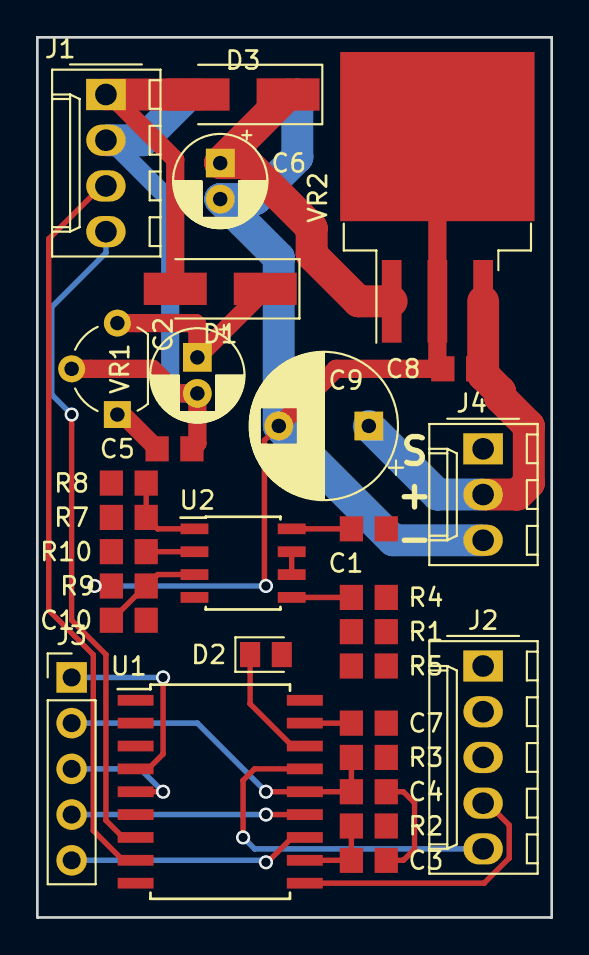
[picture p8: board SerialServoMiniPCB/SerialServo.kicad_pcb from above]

Board: 2 copper layers, 28.6 x 48.9 mm, 31 parts (1 on the bottom side), 26 nets.

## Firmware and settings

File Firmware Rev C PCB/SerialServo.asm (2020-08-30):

;====================================================================================================
;
;    Filename:      SerialServo.asm
;    Created:       4/26/2018
;    File Version:  1.1b5   8/30/2020
;
;    Author:        David M. Flynn
;    Company:       Oxford V.U.E., Inc.
;    E-Mail:        dflynn@oxfordvue.com
;    Web Site:      http://www.oxfordvue.com/
;
;====================================================================================================
;    SerialServo is sample code.
;    Controls a single robot arm joint using an R/C servo (SG90) modified
;    for continuous rotation.  Features and configurations will be added as needed.
;
;    Features: 	TTL Packet Serial
;	R/C Servo PWM output
;	Current sensing.
;	3 Buttons/LEDs for config
;	Absolute magnetic encoder
;
;Mode 0: (LED 1 = off) servo test mode, copy AN4 Pot value x 2 + 1976 to servo PWM.
;Mode 1: (LED 1 = 1 flash) servo and encoder test mode, AN4 Pot value + 950 - EncoderVal to servo dir.
;Mode 2: Basic Serial Servo, output servo pulse of ssCmdPos x 0.5uS.
;Mode 3: Absolute encoder position control. ssCmdPos = 0..4095
;Mode 4: Gripper force control.
;
;    History:
; 1.1b5   8/30/2020    Added support for Rev D PCB, Aux3...
; 1.1b4   8/26/2020    Addded kCmd_SetKp..., Fixed Batt Volts (AN1), ClampInt bug fixed.
; 1.1b3   4/10/2020    Improved Mode 3
; 1.1b2   8/11/2019	Continue fixes for 14bit encoder. New defaults Mode 3 (2950 ±100, fast, Idle center)
; 1.1b1   3/21/2019	Port for Rev C PCB
; 1.0b7   10/3/2018	Mode 3 is working for 4-wheel rover corner pivot motors.
; 1.0b6   8/18/2018	Moved analog variables to bank 1. Fast blink on error. EncoderOffset for mode3
; 1.0b5   7/23/2018	Aux IO
; 1.0b4   7/14/2018	Better defaults. Gripper mode (4).
; 1.0b3   6/19/2018	Added ssEnableFastPWM
; 1.0b2   6/3/2018	Servo current is averaged, DD DD Sync bytes and checksum.
; 1.0b1   6/1/2018	Modes 2 and 3 are working. No current limit yet.
; 1.0a3   5/31/2018    Added Speed, StopCenter.
; 1.0a2   5/25/2018	Added some more commands.
; 1.0a1   5/24/2018	It begins to work.
; 1.0d1   4/26/2018	First code.
;
;====================================================================================================
; ToDo:
;
;
;====================================================================================================
;====================================================================================================
; What happens next:
;   At power up the system LED will blink.
;   Mode 0: (LED 1 = off) servo test mode, copy AN4 Pot value to servo.
;   Mode 1: (LED 1 = 1 flash) servo  and encoder test mode, AN4 Pot value - EncoderVal to servo dir.
;   Mode 2: Basic Serial Servo, output servo pulse of CmdPos * 0.5uS.
;   Mode 3: Absolute encoder position control, Single rotation of encoder, Continuous rotation servo.
;   Mode 4: Gripper force control.
;====================================================================================================
;
;   Pin 1 (RA2/AN2) SW1/LED1 (Active Low Input/Output)
;   Pin 2 (RA3/AN3) SW2/LED2 (Active Low Input/Output)
;   Pin 3 (RA4/AN4) SW3/LED3 (Active Low Input/Output) Rev D only
;   Pin 4 (RA5/MCLR*) VPP/MCLR*
;   Pin 5 (GND) Ground
;   Pin 6 (RB0) MagEnc_CSBit (Active Low Output)
;   Pin 7 (RB1/AN11/SDA1) MISO MagEnc_DataBit (Digital Input)
;   Pin 8 (RB2/AN10/TX) TTL Serial RX
;   Pin 9 (RB3/CCP1) Pulse output for Servo
;
;   Pin 10 (RB4/AN8/SLC1) SCL1 MagEnc_CLKBit
;   Pin 11 (RB5/AN7) TTL Serial TX
;   Pin 12 (RB6/AN5/CCP2) ICSPCLK
;   Pin 13 (RB7/AN6) ICSPDAT
;   Pin 14 (Vcc) +5 volts
;   Pin 15 (RA6) MOSI MagEnc_DataBit (Digital Output)
;   Pin 16 (RA7/CCP2) LED3 (Active Low Output)(System LED)
;   Pin 17 (RA0/AN0) Current sensing analog input
;   Pin 18 (RA1/AN1) Battery voltage sensing analog input
;
;====================================================================================================
;
;
	list	p=16f1847,r=hex,W=1	; list directive to define processor
	nolist
	include	p16f1847.inc	; processor specific variable definitions
	list
;
	__CONFIG _CONFIG1,_FOSC_INTOSC & _WDTE_OFF & _MCLRE_OFF & _IESO_OFF
;
;
; INTOSC oscillator: I/O function on CLKIN pin
; WDT disabled
; PWRT disabled
; MCLR/VPP pin function is digital input
; Program memory code protection is disabled
; Data memory code protection is disabled
; Brown-out Reset enabled
; CLKOUT function is disabled. I/O or oscillator function on the CLKOUT pin
; Internal/External Switchover mode is disabled
; Fail-Safe Clock Monitor is enabled
;
	__CONFIG _CONFIG2,_WRT_OFF & _PLLEN_ON & _LVP_OFF
;
; Write protection off
; 4x PLL Enabled
; Stack Overflow or Underflow will cause a Reset
; Brown-out Reset Voltage (Vbor), low trip point selected.
; Low-voltage programming enabled
;
; '__CONFIG' directive is used to embed configuration data within .asm file.
; The lables following the directive are located in the respective .inc file.
; See respective data sheet for additional information on configuration word.
;
	constant	oldCode=0
	constant	useRS232=1
	constant	UseEEParams=1
	constant	UseAuxLEDBlinking=0
;
	constant	UseAltSerialPort=1
	constant	RP_LongAddr=0
	constant	RP_AddressBytes=1
	constant	RP_DataBytes=4
	constant	UseRS232SyncBytes=1
kRS232SyncByteValue	EQU	0xDD
	constant	UseRS232Chksum=1
	constant               UsePID=0
;
kRS232_MasterAddr	EQU	0x01	;Master's Address
kRS232_SlaveAddr	EQU	0x02	;This Slave's Address
kSysMode	EQU	.3	;Default Mode
Default_Kp	EQU	.32	;Fxd4.4 10*16
Default_Ki	EQU	0	; max gain is 255 = 15 15/16
Default_Kd	EQU	0
kGripperHC	EQU	0x04	;Gripper hysteresis
;
#Define	_C	STATUS,C
#Define	_Z	STATUS,Z
;
;====================================================================================================
	nolist
	include	F1847_Macros.inc
	list
;
;    Port A bits
PortADDRBits	EQU	b'10111111'
PortAValue	EQU	b'00000000'
ANSELA_Val	EQU	b'00000011'	;RA0/AN0, RA4/AN4
#Define                Aux0_ANSEL_Bit         ANSELA,2
#Define                Aux1_ANSEL_Bit         ANSELA,3
#Define                Aux2_ANSEL_Bit         ANSELA,4
;
#Define	RA0_In	PORTA,0	;Current, Analog Input
#Define	RA1_In	PORTA,1	;Battery Volts, Analog Input
#Define	SW1_In	PORTA,2	;SW1/LED1
#Define	SW2_In	PORTA,3	;SW2/LED2
#Define	SW3_In	PORTA,4	;SW3/LED3, n/c on Rev C
#Define	RA5_In	PORTA,5	;VPP/MCLR*
#Define	RA6_Out	PORTA,6	;MagEnc_DataBit Encoder MOSI (SPI, Digital Output)
#Define	RA7_In	PORTA,7	;LED3 (Active Low Output)(System LED)
LED1_Bit	EQU	2	;LED1 (Active Low Output)
LED2_Bit	EQU	3	;LED2 (Active Low Output)
LED3_Bit               EQU                    4
SysLED_Bit	EQU	7	;Sys_LED (Active Low Output)
#Define	SysLED_Tris	TRISA,SysLED_Bit	;Sys_LED (Active Low Output)
;
#Define	Aux0_LED1_TRIS	TRISA,LED1_Bit	;LED1 (Active Low Output)
#Define                Aux0_SW1_PORT          PORTA,LED1_Bit         
#Define	Aux0_LED1_Lat	LATA,LED1_Bit	;LED1 (Active Low Output)
;
#Define	Aux1_LED2_TRIS	TRISA,LED2_Bit	;LED2 (Active Low Output)
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

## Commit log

2018-05-03 Started PCB
    [SerialServo.kicad_pcb, SerialServo.sch]
2018-05-05 Schematic 1.0
    [SerialServo.sch]
2018-05-06 PCB ordered
    [SerialServo.kicad_pcb]
2018-05-17 it assembles
2018-05-27 testing continues
    Works as single servo position control.
2018-06-01 1.0a3
    Getting close to feature complete, Speed has a bug.
    [SerialServo.asm]
2018-06-02 This is Beta One
    Modes 2 and 3 work. No current limit yet.
2018-06-02 Current in mode 2
2018-06-04 Tested w/ 2 servos on the same UART
2018-06-04 PCb Rev A
    [SerialServo.kicad_pcb, SerialServo.sch]
2018-06-06 PCB Rev A work
    [SerialServo.kicad_pcb, SerialServo.sch]
2018-06-06 more lines
    [SerialServo.kicad_pcb]
2018-06-06 Rev A PCB is ordered
    [SerialServo.kicad_pcb]
2018-06-08 encoder cable
2018-06-08 current limit in mode3
2018-06-13 sneeking up on a robot arm controller
    [Robot Arm Model.scad]
2018-06-16 code cleanup
    [Robot Arm Model.scad]
2018-06-20 PCB Rev B
    [SerialServo.bom.csv, SerialServo.kicad_pcb, SerialServo.sch]
2018-06-20 Fast 10mS PWM enabled
2018-06-22 Started mini pcb
    [SerialServo.bom.csv, SerialServo.kicad_pcb, SerialServo.sch]
2018-07-11 began adding gripper
2018-07-25 multi-servo tests
2018-07-25 lo rez
    [Robot Arm Model.scad]
2018-08-13 Tube mounted case for rev B
    [Case.stl, CaseAndMount.scad, CommonStuffSAEmm.scad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]
2018-08-19 little things
    [SerialServo.sch]
2018-08-19 box fix
    [Case.stl, CaseAndMount.scad, Mount.stl]
2018-08-22 Encoder offset in Mode 3
2018-10-03 HiZ Tx fixed
    added diode, not doable in s/w
    [SerialServo.asm]
2019-01-20 PCB Rev C Schmatic
    [SerialServo.bom.csv, SerialServo.kicad_pcb, SerialServo.sch]
2019-02-17 ordered rev C
    [SerialServo.kicad_pcb]
2019-03-01 merging Brushed servo
2019-03-23 New Rev C works
    except for the bootloader
    [SerialServo.sch]
2019-07-30 Fractional speed brushed servo
2019-08-11 Updates for Rev C PCB
2019-08-22 Thread fix
2019-08-25 TJoy and Tracks Thread
2019-09-02 Added Lidar-Lite calc to URanger
2020-03-03 moving to MacroPIC + BLDC
2020-03-15 Added BLDC drive
2020-03-22 BLDC Servo working
2020-03-24 BLDC stats
2020-03-25 Aux Config and BLDC Servo
2020-03-28 BLDC Servo Acceleration added
2020-03-29 Work on BLDC
2020-04-07 updated bootloader
    began adding PID
2020-04-19 Packet serial to SPI
2020-04-19 SPI doesn't validate
2020-04-19 SPI to TMC4361A working
2020-04-19 Reading and writing SPI by address in hex
2020-08-25 Working on PID
2020-08-27 ClampInt bug fixed
2020-08-30 Rev D PCB
    [SerialServo.bom.csv, SerialServo.kicad_pcb, SerialServo.sch]
2020-08-30 Aux IO and AN updates
    [SerialServo.sch]
2020-08-31 Aux N init
    [SerialServo.sch]
2020-10-17 Worked on brushed motor
2021-04-04 worked on Simple Servo 16
2021-04-21 BLDC Zero
2021-07-16 worked on BLDC tester
